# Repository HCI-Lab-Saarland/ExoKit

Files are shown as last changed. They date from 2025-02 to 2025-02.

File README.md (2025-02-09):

# ExoKit: 
## A Toolkit for Rapid Prototyping of Interactions for Arm-based Exoskeletons 
### (ACM CHI 2025, Released Code)

**[Marie Muehlhaus](https://hci.cs.uni-saarland.de/people/marie-muehlhaus/)**, **[Alexander Liggesmeyer](https://cispa.de/de/people/c01alli)**, **[Jürgen Steimle](https://hci.cs.uni-saarland.de/people/juergen-steimle/)**

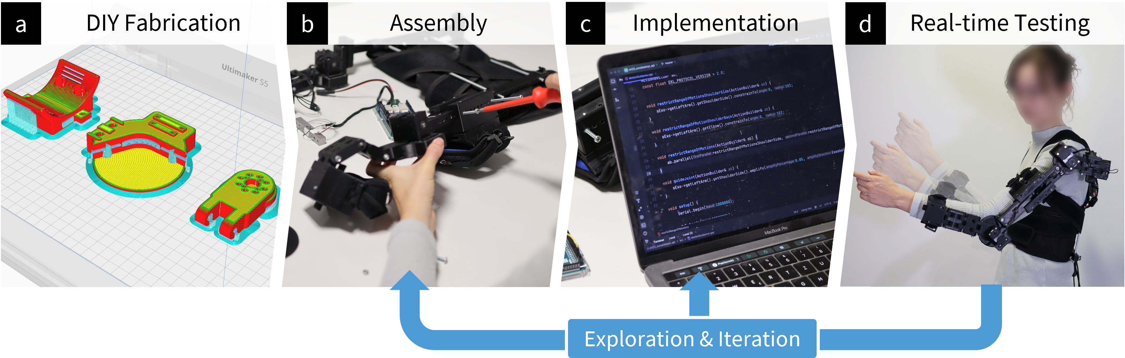
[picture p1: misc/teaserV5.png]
ExoKit Teaser Image


### Abstract
Exoskeletons open up a unique interaction space that seamlessly integrates users' body movements with robotic actuation. Despite its potential, human-exoskeleton interaction remains an underexplored area in HCI, largely due to the lack of accessible prototyping tools that enable designers to easily develop exoskeleton designs and customized interactive behaviors. We present ExoKit, a do-it-yourself toolkit for rapid prototyping of low-fidelity, functional exoskeletons targeted at novice roboticists. ExoKit includes modular hardware components for sensing and actuating shoulder and elbow joints, which are easy to fabricate and (re)configure for customized functionality and wearability. To simplify the programming of interactive behaviors, we propose functional abstractions that encapsulate high-level human-exoskeleton interactions. These can be readily accessed either through ExoKit's command-line or graphical user interface, a Processing library, or microcontroller firmware, each targeted at different experience levels.
Findings from implemented application cases and two usage studies demonstrate the versatility and accessibility of ExoKit for early-stage interaction design. 

[Read full article](https://doi.org/10.1145/3706598.3713815).

---
## Fabrication & Assembly Instructions
ExoKit comprises 3d printable modular components.

The following figure presents an overview of the main exoskeleton components:
<p float="left">
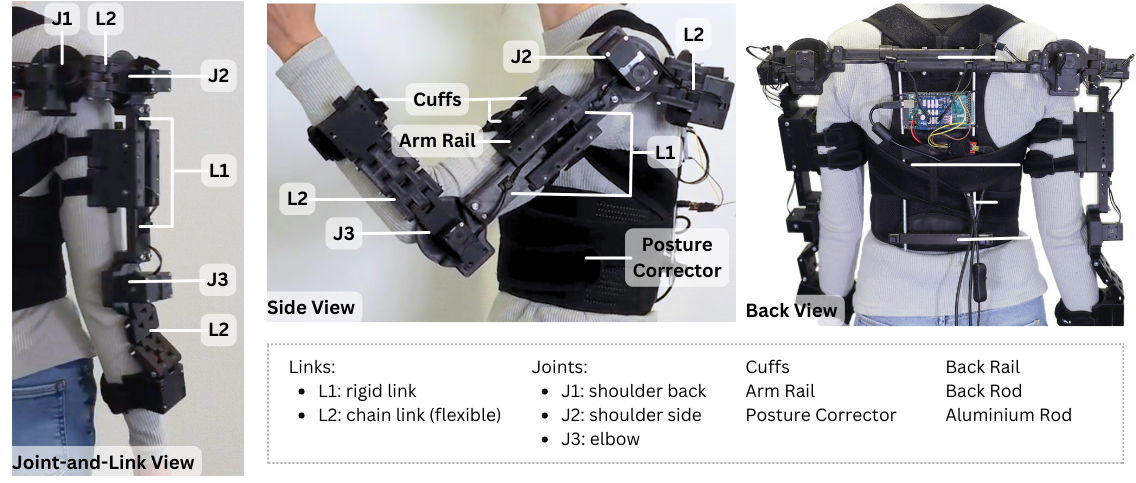
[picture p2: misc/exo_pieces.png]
  
</p>

Detailed instructions for fabrication and assembly can be found in user manual chapter 2 and 3.

## Installation Instructions and Software Usage

ExoKit provides access to pre-implemented functionalities. These comprise basic functions and five augmentation strategies. They are conceptually organized in a two-dimensional space:

<p float="left">
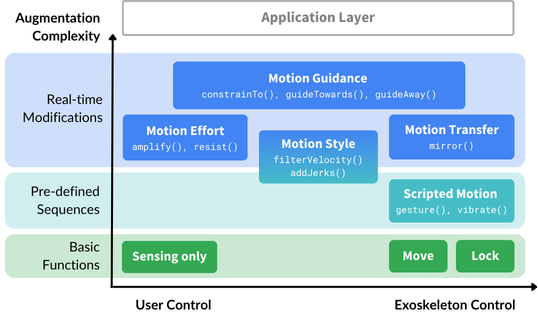
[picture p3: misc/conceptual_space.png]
  
</p>

These functionalities are accessible through different programming interfaces:
<p float="left">
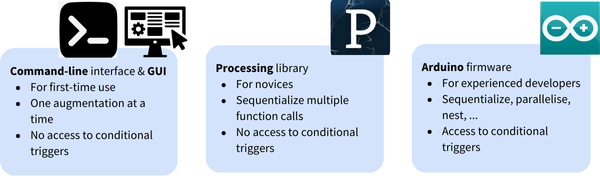
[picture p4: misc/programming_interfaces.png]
  
</p>

Please refer to user manual chapter 2 and 4-7 for more details.

---

## Citation
If you find our article, released hardware or software useful, please cite our work:

```bibtex
@inproceedings{exoKit,
author = {Muehlhaus, Marie and Liggesmeyer, Alexander and Steimle, J\"{u}rgen},
title = {ExoKit: A Toolkit for Rapid Prototyping of Interactions for Arm-based Exoskeletons},
year = {2025},
isbn = {979-8-4007-1394-1/25/04},
publisher = {Association for Computing Machinery},
address = {New York, NY, USA},
url = {https://doi.org/10.1145/3706598.3713815},
doi = {10.1145/3706598.3713815},
booktitle = {Proceedings of the 2025 CHI Conference on Human Factors in Computing Systems},
location = {Yokohama, Japan},
series = {CHI '25}
}
```

---

## Contact

Please contact [Marie Muehlhaus](https://hci.cs.uni-saarland.de/people/marie-muehlhaus/) if you have any questions about ExoKit for your use.

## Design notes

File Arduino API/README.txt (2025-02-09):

Software Setup:
1.	Download the code from this folder (“Arduino API“)
2.	Install CLION (or similar) and follow existing online guides to set up the platformIO extension. Test the successful installation with a simple Arduino program (you can find examples online).
3.	Install the required plugins in CLION:
  o	Serial Port Monitor Plugin: https://plugins.jetbrains.com/plugin/8031-serial-port-monitor
  o	PlatformIO Plugin for CLion: https://plugins.jetbrains.com/plugin/13922-platformio-for-clion  
4.	Open the project as a platformIO project with CLION.
  o	To work with the Arduino Mega, PlatformIO must be set up for megaatmega2560. We provide the suitable platformio.ini file as part of the downloaded code. The platformio.ini contains further library dependencies, such as Dynamixel2Arduino, DynamixelShield, HX711, LinkedList, TaskManagerIO.
5.	Build the project.
  o	In case of an error message about undefined references to loop and setup functions, make sure that one (and only one!) of the example programs in the src folder is commented in.
  o	In case of error messages about libraries not being available for the system, the library dependencies listed in platform.ini (“lib_deps”) might need to be adjusted to fit your system.

You can find an example video for setting up the platformIO project in CLION in the repo’s video folder (“Software Installation PlatformIO”). 

For details about the software and a quick start guide please refer to Chapter 2 of the user manual.
Fpr more details about how to program interactive behavaior with the Arduino API, please refer to Chapter 7 of the user manual.

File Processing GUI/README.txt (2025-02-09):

Processing GUI setup:
1.	Download the GitHub code from this folder (“Processing GUI”) and “Arduino API” (https://github.com/HCI-Lab-Saarland/ExoKit/tree/main/Arduino%20API). 
2.	Download Processing. The authors used version 4.3.
3.	Follow the installation guide for the Arduino API.
4.	Open processing_gui.pde.

The user manual provides further explanation on the usage of the GUI and an example of how to configure the exoskeleton in the Arduino API accordingly (Chapter 5).
All functions and parameters available in the GUI are documented in the user manual (Chapter 5).

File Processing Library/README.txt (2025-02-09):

Processing Library setup:
1.	Download the GitHub code from this folder (“Processing Library”) and “Arduino API” (https://github.com/HCI-Lab-Saarland/ExoKit/tree/main/Arduino%20API). 
2.	Download Processing. The authors used version 4.3.
3.	Install the library.
4.	Follow the installation guide for the Arduino API.

The user manual provides further explanation on the usage of the library and an example of how to configure the exoskeleton in the Arduino API accordingly (Chapter 6).
All functions, signatures and parameters available in the library are documented in the user manual (Chapter 6).

The exokit Processing library comes with one sample sketch, which shows how to configure an exoskeleton and call functions.
Prerequisites for successfully running the example sketch:
- The physical prototype is correctly configured (right arm with active shoulder side and elbow joints).
- The exoskeleton is configured correctly in the Arduino API and the serial connection is active.
- The correct serial port is entered in the Processing code.
The user manual provides an explanation and example of how to configure the exoskeleton in the Arduino API accordingly (Chapter 6)

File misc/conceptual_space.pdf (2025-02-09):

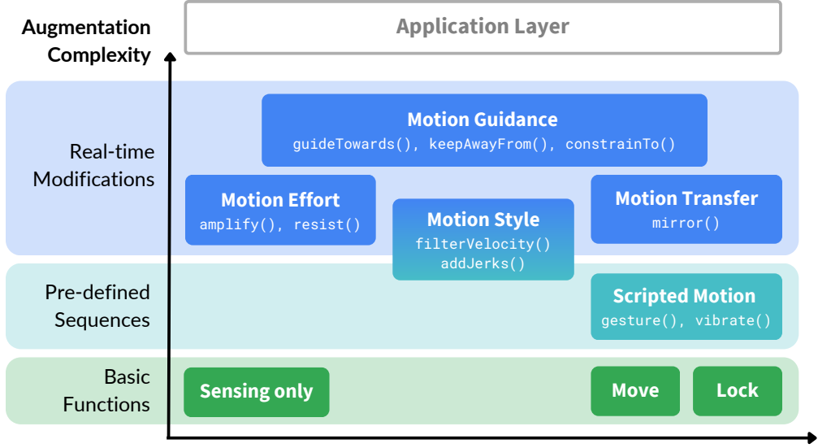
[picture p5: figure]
Sensing only; Move; Lock; Motion Effort; amplify(), resist(); Motion Style; filterVelocity() addJerks(); Motion Transfer; mirror(); Motion Guidance; Application Layer; Scripted Motion; gesture(), vibrate(); Basic Functions; Pre-defined Sequences; Real-time Modifications; Augmentation Complexity

guideTowards(), keepAwayFrom(), constrainTo()

User Control | Exoskeleton Control

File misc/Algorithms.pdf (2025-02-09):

## ExoKit: A Toolkit for Rapid Prototyping of Interactions for Arm-based Exoskeletons

Marie Muehlhaus, Alexander Liggesmeyer, J¨urgen Steimle
Supplemental Material: Algorithms

This supplemental material contains the pseudocode for the algorithms presented in section 4 of the paper, organized by the higher-level motion augmentation strategies. The algorithms build on the following basic functions:

- moveTo(ji
, θi

, υ) moves the joint ji towards a target angle θi with a user-specified velocity υ. All angles are absolute unless explicitly stated otherwise. The function internally checks if the goal angle is beyond a joint’s calibrated range of motion (RoM). If so, the joint would be moved just towards the bound but never beyond. Unless the torque was updated before

(see update torque(ji

, τ )), the motor will be moved with the largest possible torque.

- lock(ji) locks the joint ji
in place. unlock(ji) unlocks the joint ji
- update torque(ji
, τ ) ensures the motor of joint ji
is moving with the specified torque τ ; if τ = 0, then the the torque is disabled. torque is enabled(ji) and torque is disabled(ji) indicate whether τ > 0 and τ = 0, respectively.
- get angle(ji), get velocity(ji), get direction(ji) return the current joint angle, velocity, and movement direction (extension/adduction, flexion/abduction, or both) of ji
- get max velocity(ji) returns the maximum velocity that the motor attached to ji can provide.
- get upper RoM(ji) and get lower RoM(ji) return the maximum and minimum angles of ji

’s calibrated range of motion

- is moving(ji) indicates whether ji
is currently moving.
- parallel(s1, . . . , sk) executes k statements s1, . . . , sk in parallel (e.g., two moveTo(·) at the same time).

In the following, we refer to the joint modules attached to the elbow (flexion-extension), side (flexion-extension) and back (abduction-adduction) of the shoulder as jelbow, jsside, and jsback. Without loss of generality, in the following, we assume that (1) D ∈ {“extension”, “flexion”, “both”} for any direction D and (2) ji ∈ {jelbow, jsside}. We leave out code for D ∈ {“adduction“, “abduction“} and ji = jsback which works analogously to extension and flexion and the other joints.

Further, we decided on the values of constants in the code after doing preliminary tests in the research team. This refers to, for instance, dirChangeSuspensionT ime (amplify) and linearGrowth (resist).

All algorithms except the one for the waving gesture can also have an optional condition as input. In these algorithms, while-loops will run until they are aborted through this user-defined condition, such as a timer, or an emergency shutdown. To keep the pseudocode abstract, we do not include this input in the require parameters and only state the conditions explicitly if needed.

Please note that the algorithms represent the logic of the implemented functions in the form of readable pseudocode, which abstracts away the details of specific programming languages. Our implementation was realised in C++ with an event-based architecture and dedicated Condition and Action classes. The pseudocode below therefore looks different from the actual program structure.

## 1 Scripted Motions

Wave This function executes a sequence of movements to perform a waving gesture with the arm.

Algorithm 1 Wave
Require: exoskeleton arm with active joints at the elbow, shoulder side and back: jelbow,jsback,

jsside
1: parallel(moveTo(jelbow, 90, 70), moveTo(jsside, 0, 70), moveTo(jsback, 90, 70))

2: parallel(lock(jsside), lock(jsback), moveTo(jelbow, 45, 50))
3: moveTo(jelbow, 90, 50)
4: moveTo(jelbow, 45, 50)
5: moveTo(jelbow, 90, 50)
6: moveTo(jelbow, 45, 50)

7: parallel(unlock(jsside), unlock(jsback))

Vibrate This function generates a vibrating sensation at a joint ji through rapid back-and-forth movements of adjustable amplitude and frequency. The function will loop until aborted. An abort can be triggered by a user defined condition or an emergency shutdown.

Algorithm 2 Vibrate
Require: joint ji

, amplitude amp, frequency f 1: υrequired ← min(4f · amp, get max velocity(ji)) ▷ ensure that υrequired does not exceed the max. available velocity of ji
2: while not aborted do ▷ the loop will run until it is aborted through a user-defined condition, such as a timer, or an emergency shutdown
3: | moveTo(ji

, 2 · amp, υrequired, relative)

4: | moveTo(ji

, −2 · amp, υrequired, relative)

## 2 Motion Transfer

Mirror The mirror function facilitates motion transfer between two exoskeletons or joint instances, where in every time interval, the state of the source joints js is read and the target joints jt are moved accordingly. Users can optionally scale the motion up or down by a user-defined factor, while the moveTo(·) function internally ensures that the scaled motion does not exceed the user’s calibrated limits of their range of motion. The function runs in a loop until it is aborted.

Algorithm 3 Mirror
Require: target joint jt

, source joint js, scale factor f
1: while not aborted do
2: | moveTo(jt

, f · get angle(js), get max velocity(ji))

## 3 Effort Modulation

Amplify Amplify applies a torque in a user’s inherent motion, while preserving the user’s ability to freely navigate in space. The function includes parameters that allow designers to adjust the assistive torque τamp and to specify whether the strategy should be continuously active or only triggered when the user moves in a certain direction D ∈ {“flexion”, “extension”, “both”}. To avoid false activations triggered by slight jerks of the user or amplifying the user beyond a safe speed, the function additionally includes parameters that define the minimum and maximum speed where the amplification should start or pause respectively. The function runs in a loop until it is aborted.

Algorithm 4 Amplify
Require: joint ji

, amplifying torque τamp, supported movement direction D, minimum velocity to start amplification υstart, max. velocity to which arm should be amplified υstop
1: dirChangeSuspensionT ime ← 200 ▷ a constant that tunes the sensitivity to direction changes (in ms)
2: lastDirChangeT ime, lastT orqueEnable ← 0
3: f irstStep ← true
4: currentDirIsFlex ← f alse
5: while not aborted do
6: | if (|get velocity(ji)| > |υstop|) then
| /* stop amplification because ji moves too fast */
7: | update torque(0)
8: | else if (|get velocity(ji)| > |υstart| ∧ D ∈ {get direction(ji)} ∪ {“both′′} then
| /* ji moves sufficiently fast in desired direction */
9: | dirIsFlexU pdated ← get direction(ji) = flexion
10: | if currentDirIsFlex ̸= dirIsFlexU pdated then
| /* because direction has changed, we pause the amplification */
11: | currentDirIsFlex ← dirIsFlexU pdated
12: | if f irstStep then
13: | f irstStep ← f alse
14: | else
15: | lastDirChangeT ime ← millis()
16: | update torque(0)
17: | if lastDirChangeT ime + dirChangeSuspensionT ime < millis() then
| /* because enough time has passed between direction change and now, we resume ampli-
| fication */
18: | if torque is disabled(ji) then
| /* amplify by letting ji pull the user with τamp towards the end of user’s RoM. */
19: | update torque(ji , τamp)
20: | lastT orqueEnable ← millis()
21: | if currentDirIsFlex then
22: | moveTo(ji , get upper RoM(ji), υstop)
23: | else
24: | moveTo(ji , get lower RoM(ji), υstop)
25: | else if lastT orqueEnable + dirChangeSuspensionT ime < millis() then
| /* eventually pause amplification if ji moves too slow or in opposite direction */
26: | update torque(0)

Resist Resist applies a torque opposite to a user’s inherent motion, while preserving the user’s ability to freely navigate in space. The function includes parameters that allow designers to adjust the resistive torque τres and to specify whether the strategy should be continuously active or only triggered when the user moves in a certain direction D ∈ {“flexion”, “extension”, “both”}. To avoid that the user is slowed down below a specific speed, the function additionally includes a parameter that defined the minimum speed. The function runs in a loop until it is aborted.

Algorithm 5 Resist
Require: joint ji
, resisting torque τres, supported movement direction D, min. velocity to which arm should be slowed down υstop
1: linearGrowth ← 100 ▷ a constant that tunes the adaptation to velocity changes (in deg/sec) 2: f irstStep ← true
3: currentDirIsFlex ← f alse
4: while not aborted do
/* adapt the resistance to ji’s velocity by τfraction ∈ [0, 1] percent; the slower the motion, the weaker the resistance, so that the user is not abruptly slowed down when the resistance is triggered. */
5: | τfraction ← min(1, max(0, |get velocity(ji)|−|υstop|
|υstop|+linearGrowth | ))
6: | τadapt ← τres · τfraction
7: | if |get velocity(ji)| < |υstop| then | ▷ pause resistance if ji is too slow
8: | update torque(0)
9: | else if D ∈ {get direction(ji)} ∪ {“both′′} then
/* if ji moves sufficiently fast in desired direction, provide resistance; if user is not moving anymore in the same direction as in the previous loop iteration, update behavior */
10: | dirIsFlexU pdated ← get direction(ji) = “flexion”

/* resist by letting ji continuously try to push the user towards ji, making it hard to
| move away from this fix point */
11: | update torque(ji
| , τadapt) | ▷ update applied torque now
12: | if torque is disabled(ji) then
13: | moveTo(ji
| , get angle(ji), υstop) | ▷ torque was disabled, so update fix point
14: | else if currentDirIsFlex ̸= dirIsFlexU pdated then
15: | currentDirIsFlex ← dirIsFlexU pdated
16: | if firstStep then
17: | f irstStep ← f alse
18: | else
19: | moveTo(ji
| , get angle(ji), υstop) | ▷ direction changed, so update fix point
20: | else
21: | update torque(0)

## 4 Motion Style

Jerks The jerk function introduces short exoskeleton movements at a user-specified velocity, with varying magnitude and at varying time intervals, creating brief perturbations in the user’s inherent motion. The loop runs until aborted or the user-specified number of jerks is performed.

Algorithm 6 Jerk

Require: joint ji

, min./max. jerk size θminJerk/θmaxJerk, min./max. time interval between jerks tmin/tmax, jerk velocity υ, number of jerks nrJerks
1: lastLoopRun, lastJerk ← millis()
2: currentW aitDuration ← 0
3: jerksP erformed ← 0
4: while not aborted ∧ jerksP erformed < nrJerks do
5: | currentT ime ← millis()
6: | deltaLastLoopRun ← currentT ime − lastLoopRun
7: | lastLoopRun ← currentT ime
8: | if ¬is moving(ji) then | ▷ no jerks if user does not move
9: | lastJerk ← lastJerk + deltaLastLoopRun
10: | continue
11: | if ¬(currentT ime > lastJerk + currentW aitDuration) then ▷ not yet time for the next
| jerk
12: | continue
13: | lastJerk ← millis()
14: | currentW aitDuration ← random([tmin, tmax])
15: | valid ← true
16: | repeat
/* randomly search for a valid choice for θjerk, i.e., within the user’s specifications */
17: | jerkDirection ← random({“flexion”, “extension”})
18: | θjerk ← random([θminJerk, θmaxJerk])
19: | if jerkDirection = “extension” then
20: | θjerk ← −θjerk | ▷ a jerk towards extension decreases current angle
21: | if (get angle(ji) + θjerk > get upper RoM(ji)) ∨ (get angle(ji) + θjerk <
| get lower RoM(ji)) then
/* if jerk moves out of calibrated RoM, jerk is invalid */
22: | valid ← false
23: | until valid
24: | moveTo(ji , get angle(ji) + θjerk, υ)
25: | jerksP erformed ← jerksP erformed + 1

Filter Speed Filter speed tries to keep a user’s motion speed within a pre-defined range, by applying assistive torques if they are too slow or resisting ones if they are moving too fast. Designers can fine-tune these effects by setting the velocity range, the forces applied to maintain it and by specifying whether the strategy should be continuously active or only triggered when the user moves in a certain direction D ∈ {“flexion”, “extension”, “both”}. The function runs in a loop until it is aborted.

Algorithm 7 Filter Speed
Require: joint ji

, min. and max. speed υmin and υmax, supported movement direction D, amplifying/resisting torque during flexion τampF lex/τresF lex, amplifying/resisting torque during

extension τampExt/τresExt
1: while not aborted do
2: | if D ∈ {“both”, “extension”} then | ▷ set filter only for the right direction(s)
3: | if |get velocity(ji)| > |υmax| then | ▷ as long as user is too fast, resist
4: | Resist(ji

, τresExt, D, |υmax|) with abort condition |get velocity(ji)| ≤ |υmax| ∨
| get direction(ji) ̸= “extension”
5: | else if |get velocity(ji)| < |υmin| then | ▷ as long as user is too slow, amplify
6: | Amplify(ji

, τampExt, D, 10, |υmin|) with abort condition |get velocity(ji)| ≥
| |υmin| ∨ get direction(ji) ̸= “extension”
7: | if D ∈ {“both”, “flexion”} then
8: | if |get velocity(ji)| > |υmax| then
9: | Resist(ji

, τresF lex, D, |υmax|) with abort condition |get velocity(ji)| ≤ |υmax| ∨

| get direction(ji) ̸= “flexion”
10: | else if |get velocity(ji)| < |υmin| then
11: | Amplify(ji

, τampF lex, D, 10, |υmin|) with abort condition |get velocity(ji)| ≥
| |υmin| ∨ get direction(ji) ̸= “flexion”

## 5 Motion Guidance

Constrain to This function constrains the range of motion of a joint ji to an area around an absolute angle θi with range ϵ. As soon as the user attempts to move beyond this range, the exoskeleton tries to move the user back to the boundary, thereby keeping the joint within the specified limits. The function runs in a loop until it is aborted.

Algorithm 8 Constrain to
Require: joint ji

, central angle θi
, range ϵ
1: while not aborted do
2: | if get angle(ji) ≤ θi − ϵ then
3: | goalAngle ← θi − ϵ + 0.55 | ▷ move the user back into the allowed area
4: | moveTo(ji

, goalAngle, get max velocity(ji))
5: | else if get angle(ji) ≥ θi + ϵ then
6: | goalAngle ← θi + ϵ − 0.55
7: | moveTo(ji

, goalAngle, get max velocity(ji))

Guide Towards This function guides the user towards an area centered around θi with range ϵ. The exoskeleton applies assistive torques τamp when moving towards the desired area and resists with τres otherwise. The function runs in a loop until it is aborted.

Algorithm 9 Guide towards
Require: joint ji

, central angle θi

, range ϵ, amplifying torque τamp, resisting torque τres 1: while not aborted do
2: | if get angle(ji) ≥ θi + ϵ then | ▷ if above upper bounds
3: | while get angle(ji) ≥ θi + ϵ do | ▷ not back in motion range
/* to get back in the area, resist during flexion and amplify during extension */
4: | if get direction(ji) = “flexion” then | ▷ If user moves further away, resist
5: | Resist(ji

, τres, “flexion”, 0) with abort condition get direction(ji) ̸= “flexion”
6: | else | ▷ If user approaches the area, amplify
7: | Amplify(ji

, τamp, “extension”, 0, get Max Velocity(ji)) with abort condition get angle(ji) < θi + ϵ ∨ get direction(ji) ̸= “extension”
8: | else if get angle(ji) ≤ θi − ϵ then | ▷ if below lower bounds
9: | while get angle(ji) ≤ θi + ϵ do | ▷ not back in motion range
/* to get back in area, resist extension and amplify flexion */
10: | if get direction(ji) = “flexion” then
11: | Amplify(ji

, τamp, “flexion”, 0, get Max Velocity(ji)) with abort condition

get angle(ji) > θi + ϵ ∨ get direction(ji) ̸= “flexion”
12: | else
13: | Resist(ji

, τres, “extension”, 0) with abort condition get direction(ji) ̸=
| “extension”

Guide Away This function keeps ji away from the area around θi
, applying resistance with torque τres if the user is approaching the area and assistive torques τamp otherwise. The function runs in a loop until it is aborted.

Algorithm 10 Guide away
Require: joint ji

, central angle θi

, range ϵ, amplifying torque τamp, resisting torque τres 1: while not aborted do

2: | if get angle(ji) ≥ (θi − ϵ) ∧ get angle(ji) ≤ (θi + ϵ) then
/* if ji is in dead area, move it out */
3: | if get angle(ji) ≥ θi then | ▷ if closer to upper side, move out there
4: | moveTo(ji , θi + ϵ + 0.55, 0)
5: | else
6: | moveTo(ji , θi − ϵ − 0.55, 0)
7: | else
/* if ji not in dead area, use amplify an resist to keep ji away from it */
8: | if get angle(ji) > θi + ϵ then
9: | while get angle(ji) > θi + ϵ do ▷ above dead area, prevent user from moving to-
| ward it
10: | if get direction(ji) = “flexion” then
/* support user when moving away from the dead area */
11: | Amplify(ji

, τamp, “flexion”, 0, get Max Velocity(ji)) with abort condition

| get direction(ji) ̸= “flexion”
12: | else
/* prevent user when moving towards the dead area */
13: | Resist(ji

, τres, “extension”, 0) with abort condition get angle(ji) ≤ θi +ϵ∨
| get direction(ji) ̸= “extension”
14: | else if get angle(ji) < θi − ϵ then
15: | while get angle(ji) < θi − ϵ do ▷ below dead area, prevent user from moving to-
| ward it
16: | if get direction(ji) = “flexion” then
17: | Resist(ji

, τres, “flexion”, 0) with abort condition get angle(ji) ≥ θi − ϵ ∨

| get direction(ji) ̸= “flexion”
18: | else
19: | Amplify(ji

, τamp, “extension”, 0, get Max Velocity(ji)) with abort condition get direction(ji) ̸= “extension”

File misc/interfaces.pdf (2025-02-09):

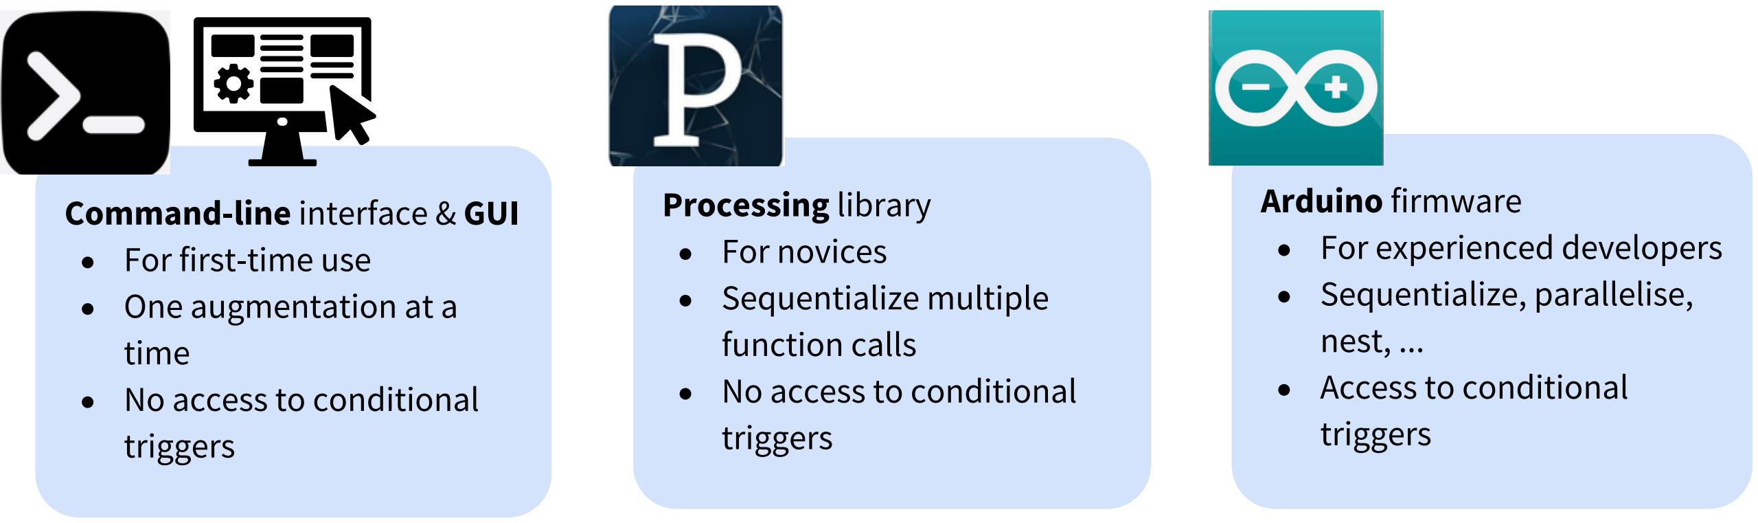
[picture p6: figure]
Processing library For novices Sequentialize multiple function calls No access to conditional triggers; Command-line interface & GUI For first-time use One augmentation at a time No access to conditional triggers; Arduino firmware For experienced developers Sequentialize, parallelise, nest, ... Access to conditional triggers

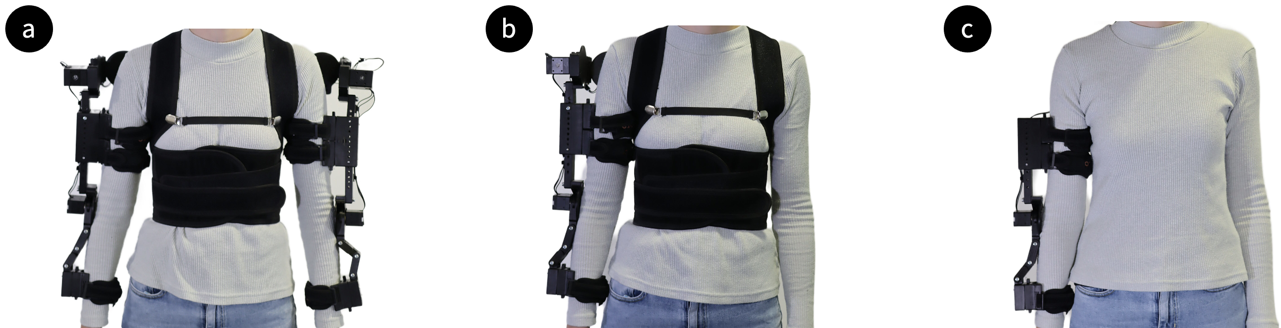
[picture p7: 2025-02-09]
misc/exo_configurations.png

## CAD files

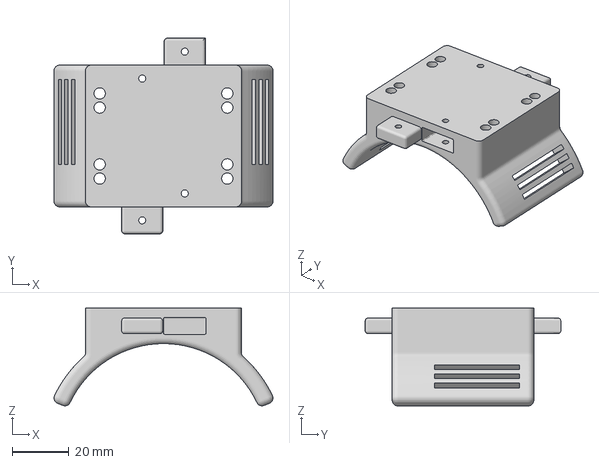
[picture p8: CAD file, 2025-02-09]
3d-prints/forearm_cuff.3mf
77.2 x 69.0 x 34.4 mm

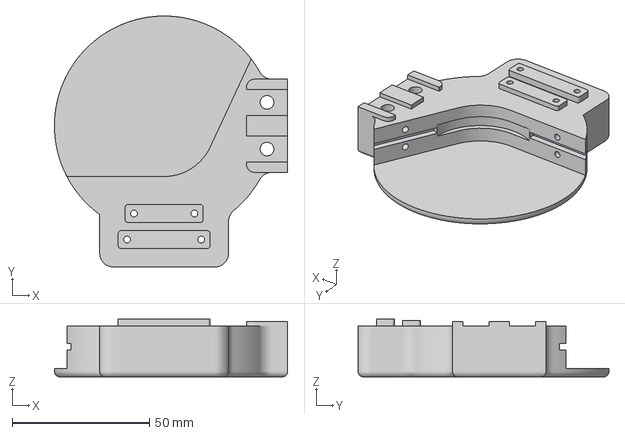
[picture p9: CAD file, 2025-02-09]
3d-prints/left-arm/joint_elbow_l.3mf
85.0 x 91.5 x 21.1 mm

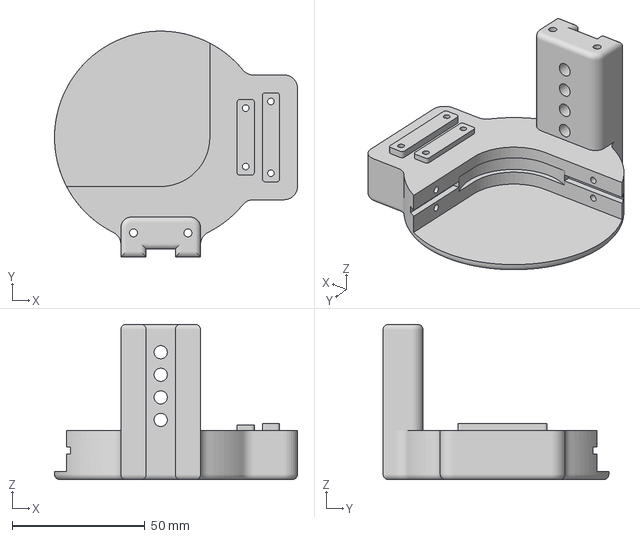
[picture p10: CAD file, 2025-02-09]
3d-prints/right-arm/joint_shoulder_back_r.3mf
91.5 x 85.0 x 58.5 mm

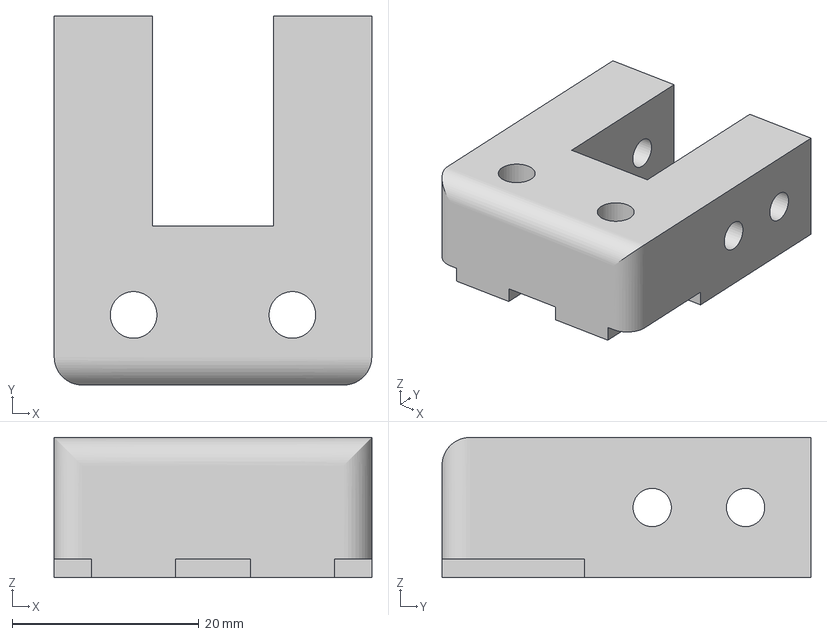
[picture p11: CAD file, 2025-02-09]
3d-prints/loadcell_adapter_joint.3mf
34.0 x 39.5 x 15.0 mm

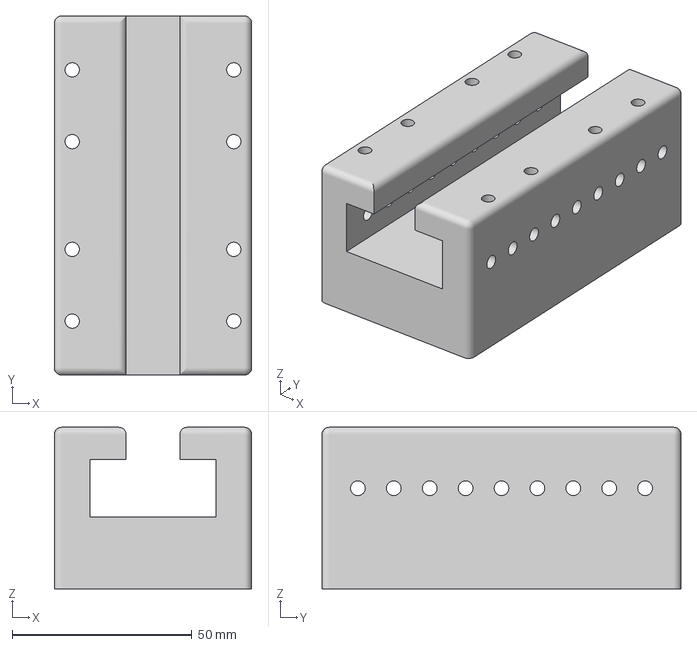
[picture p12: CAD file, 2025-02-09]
3d-prints/arm_rail.3mf
55.0 x 100.0 x 45.0 mm

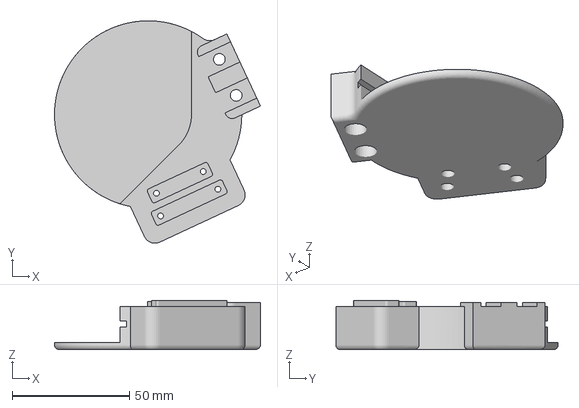
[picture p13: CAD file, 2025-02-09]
3d-prints/left-arm/joint_shoulder_side_l.3mf
88.0 x 94.9 x 21.1 mm

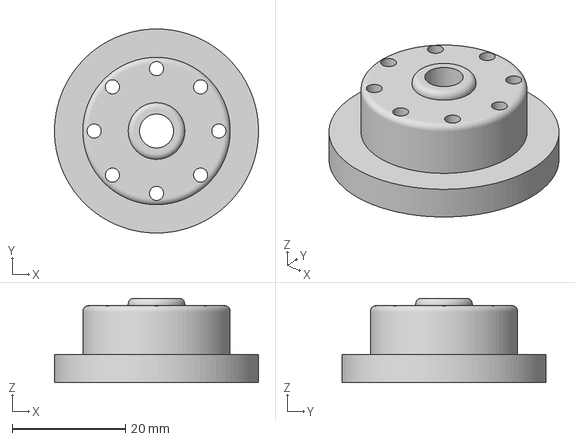
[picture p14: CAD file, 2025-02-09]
3d-prints/servo_dummy_rotor.3mf
36.0 x 36.0 x 14.9 mm

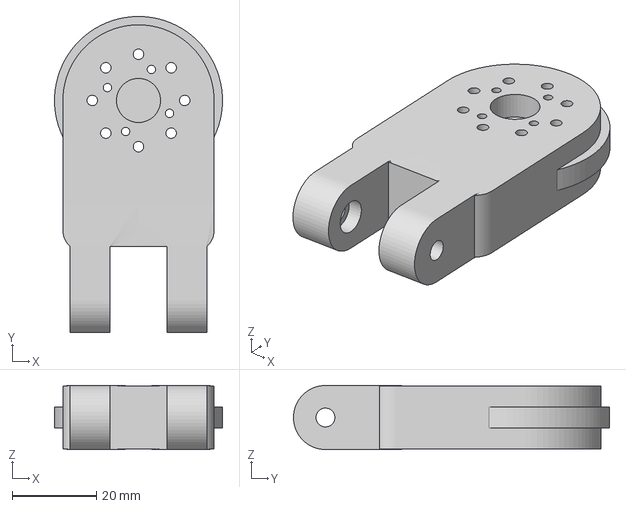
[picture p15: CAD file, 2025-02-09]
3d-prints/rotor.3mf
40.0 x 75.2 x 15.2 mm

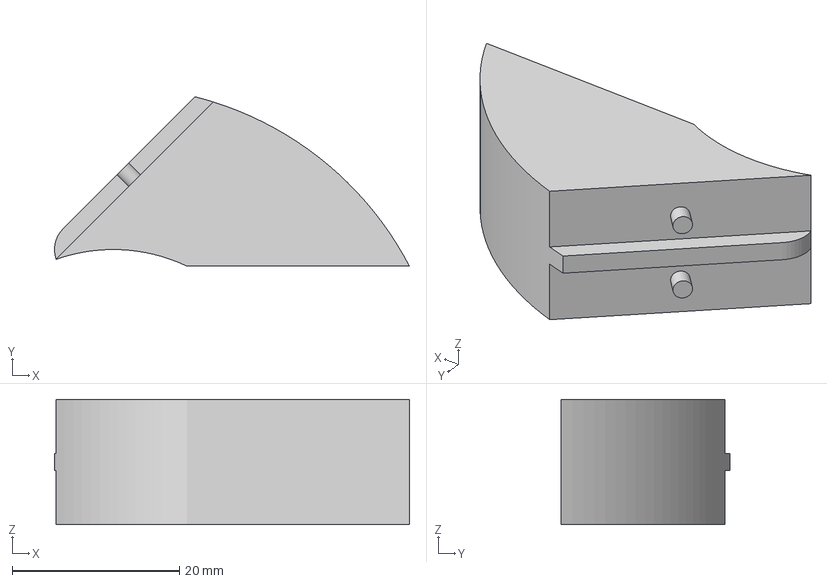
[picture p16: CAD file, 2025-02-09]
3d-prints/restriction_45.3mf
42.5 x 20.3 x 15.0 mm

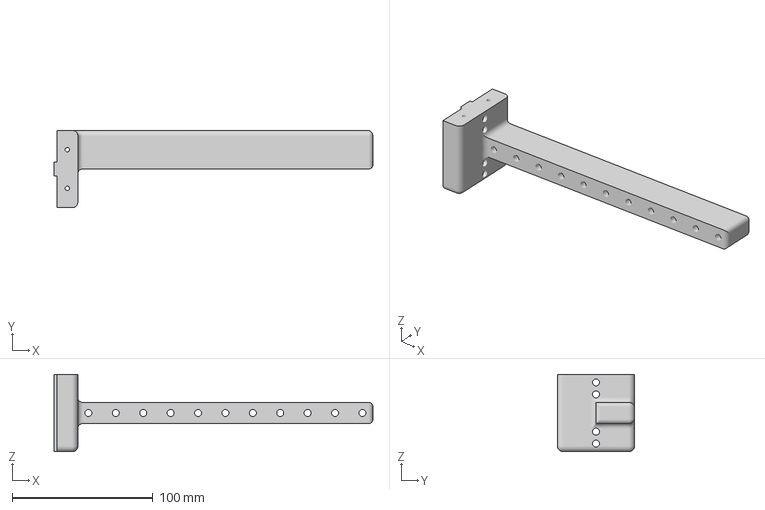
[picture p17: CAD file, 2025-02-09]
3d-prints/back_rail.3mf
227.0 x 55.0 x 55.0 mm

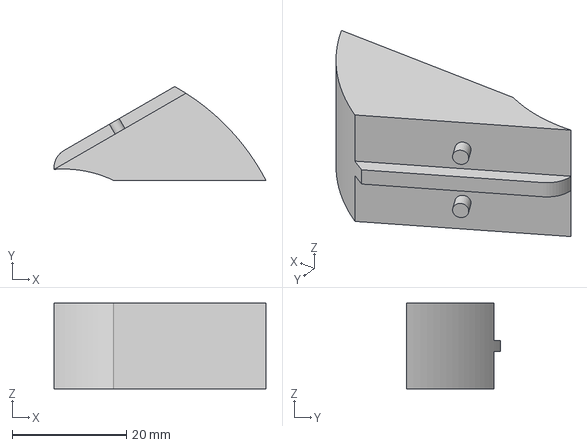
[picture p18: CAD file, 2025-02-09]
3d-prints/restriction_30.3mf
37.1 x 16.4 x 15.0 mm

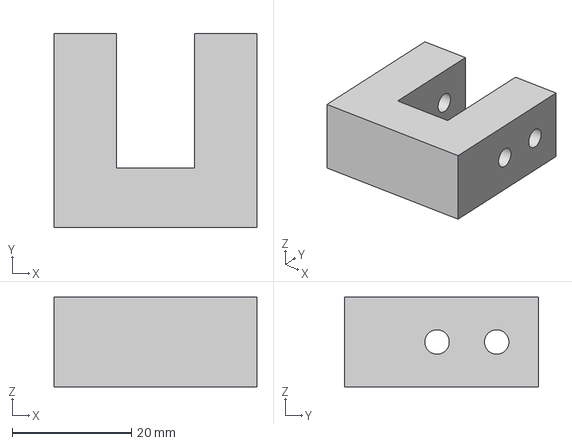
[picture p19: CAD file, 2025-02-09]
3d-prints/loadcell_adapter_rail.3mf
34.0 x 32.5 x 15.0 mm

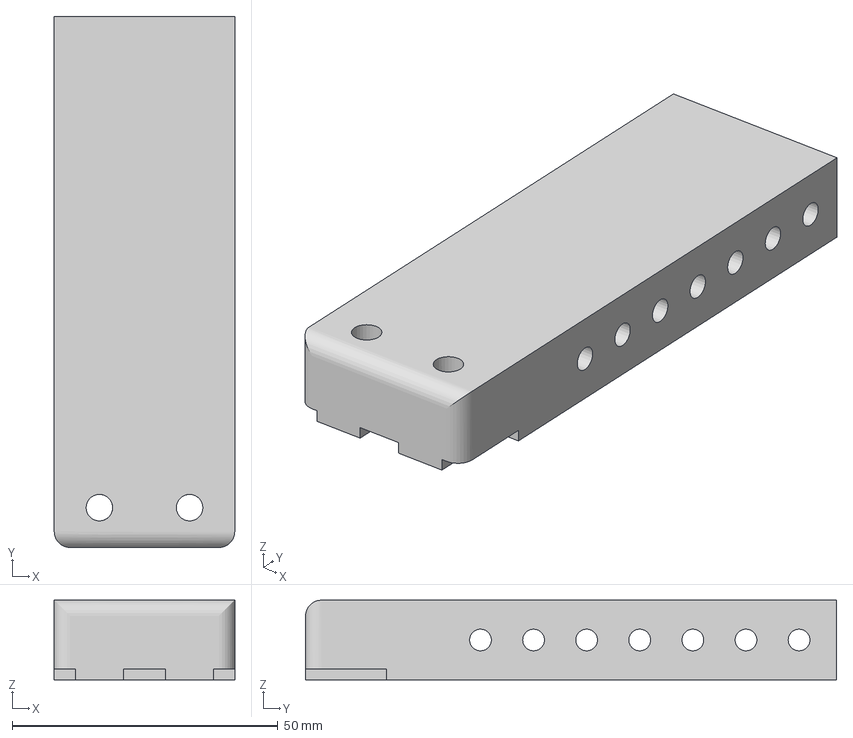
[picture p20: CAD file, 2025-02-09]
3d-prints/joint_rod_long.3mf
34.0 x 100.0 x 15.0 mm

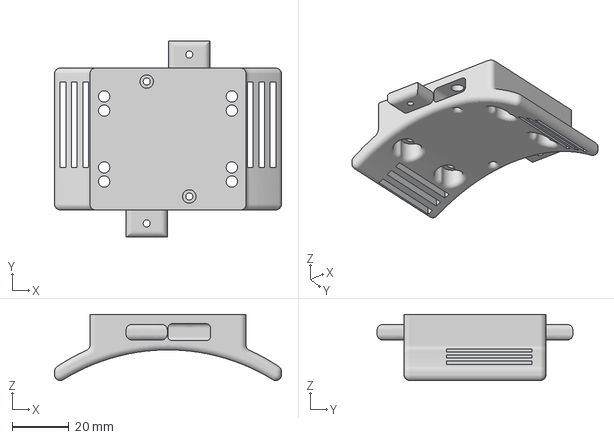
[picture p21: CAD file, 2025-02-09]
3d-prints/arm_cuff_upper_arm.3mf
80.0 x 69.0 x 23.3 mm

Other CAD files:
3d-prints/left-arm/joint_shoulder_back_l.3mf
3d-prints/right-arm/joint_elbow_r.3mf
3d-prints/right-arm/joint_shoulder_side_r.3mf
3d-prints/chain_mf.3mf
3d-prints/chain_mm.3mf
3d-prints/forearm_chain_adapter.3mf
3d-prints/lower_back_rail.3mf
3d-prints/restriction_20.3mf
3d-prints/servo_dummy_outer.3mf

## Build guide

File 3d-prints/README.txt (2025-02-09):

The 3d models were designed with Autodesk Fusion 360. We fabricated the 3D-printed parts with an Ultimaker S5 printer, using ABS filament. We used 100% infill with an octet infill pattern, a normal support structure and 2 mm wall thickness. 

To build the back construction, print:
	2x back_rail
	1x lower_back_rail

To build a 3 DoF actuated left arm (right arm analogous), print:
	Joints: 1x joint_elbow_l, 1x joint_shoulder_back_l, 1x joint_shoulder_side_l, 3x rotor
	Cuffs: 2x arm_cuff_upper_arm, 1x forearm_cuff (the cuff for the forearm is smaller than the upper arm cuff)
	Links: 1x arm_rail, 2x joint_rod_long, 1x forearm_chain_adapter, multiple chain_mf and chain_mm (we recommend at least two chain segments of each type)

If passive joint modules are needed, print:
	1x servo_dummy_outer
	1x servo_dummy_rotor
	1x rotor

If a load cell should be deployed at the upper arm, also print:
	1x loadcell_adapter_joint 
	1x loadcell_adapter_rail 

For more fabrication and assembly information, please refer to the user manual (Chapter 2 & 3).

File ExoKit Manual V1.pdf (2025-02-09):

# EXOKIT

## A TOOLKIT FOR RAPID PROTOTYPING OF INTERACTIONS FOR ARM-BASED EXOSKELETONS

## MARIE MUEHLHAUS, ALEXANDER LIGGESMEYER, JÜRGEN STEIMLE

## USER MANUAL

VERSION 1.0 (NOV 2024)

EXOKIT | A Toolkit for Rapid Prototyping of Interactions for Arm-based Exoskeletons

Project Webpage (including video, link to 3d models, code etc): https://hci.cs.uni-saarland.de/exokit/

Reference:
If you use this toolkit, please reference the scientific publication as follows:
Marie Muehlhaus, Alexander Liggesmeyer, Jürgen Steimle. ExoKit: A Toolkit for Rapid Prototyping of Interactions for Arm-based Exoskeletons. In Proceedings of the 2025 CHI Conference on Human Factors in Computing Systems (CHI ‘25). Yokohama, Japan.
DOI: https://doi.org/10.1145/3706598.3713815

## 1 Table of Contents

### 6 NEXT STEPS IN DESIGN: IMPLEMENT MOTION SEQUENCES WITH THE PROCESSING

7 DEEP DIVE: IMPLEMENTING COMPLEX INTERACTIONS WITH THE ARDUINO LIBRARY......49

APPENDIX E: TERMINAL FUNCTION CALLS | 91

# 1 Introduction

## 1.1 Overview

Exoskeletons open up exciting possibilities for novel interactions that assist, modify, or constrain physical body movements. These wearable devices can be used in Human-Computer Interaction (HCI) research for applications such as motion capture, delivering haptic feedback in virtual reality (VR), and facilitating skill transfer between individuals. For instance, an exoskeleton might serve as a wearable tutor, teaching novices to perform sports like learning a perfect golf swing, or it might enhance safety in hazardous environments, such as preventing accidents on construction sites.

However, the development of functional human-exoskeleton interactions is complex, requiring expertise in mechanical design, motion control, and interaction design. ExoKit is a do-it-yourself toolkit designed to empower designers, makers, and hobbyists in prototyping low-fidelity, functional arm-based exoskeletons. Targeted at users with basic programming and electronics skills, ExoKit offers:

- Modular hardware components for sensing and actuating shoulder and elbow joints. These components are designed to be easy to fabricate, assemble, and reconfigure for customized applications.
- Programming interfaces that simplify programming interactive behaviors.

ExoKit specifically supports users in the early stages of prototyping to creatively explore diverse ideas. Once a promising interaction concept is identified, users can transition to higher-fidelity hardware and software solutions.

Chapter Overview

Chapter 1 provides an introduction to ExoKit’s purpose, some relevant background to human anatomy, application examples to inspire novel users, and recommendations for safe use.

Chapter 2 provides an overview of the required software and hardware, the fabrication and installation steps, and a quick start guide that guides novel users through the basic setup and usage of the hardware in conjunction with the software.

Chapter 3 introduces the modular hardware components, how to combine them, and how to wire the associated sensors and actuators.

Chapter 4 gives an overview of the offered software abstractions and libraries.

ExoKit is an open-source toolkit for low-fi prototyping. We invite the community to use,

Chapter 5-7 explain the usage of the Processing GUI, library, and Arduino API, respectively. It contains guidance on the setup, all function signatures, parameter explanations, sample code and troubleshooting guides. It is recommended to start with the GUI, then move on to the other libraries. It is not necessary to read a chapter in a linear fashion, but to get an overview of the available functions and then use them as needed.

Chapter 8 provides the code of four application examples presented in the published paper.

The appendices include a glossary, a debugging script when working with position encoders to ensure they are set up correctly, a sample script for streaming sensor data including load cell data, a cheat sheet of compatible motor properties and the terminal commands for the command line interface.

## 1.2 Brief Background on Human Anatomy

Understanding the biomechanics of the human upper limbs is crucial for designing effective exoskeletons. Several key properties of the upper limb's anatomy and movement capabilities are particularly relevant in this context. These include the joints’ degrees of freedom (DoFs), range of motion (RoM), and torque settings.

The shoulder joint possesses three DoFs, enabling the following movements: abduction-adduction, flexion-extension, and medial-lateral rotation. The elbow, on the other hand, has two DoFs, allowing for flexion-extension and rotation of the forearm. ExoKit currently supports flexion-extension movements in both the shoulder and elbow (see below Figure b, c), as well as abduction-adduction in the shoulder (Figure a).

The RoM of a joint defines the maximum arc through which the joint can move. These ranges can vary based on factors such as individual anatomical differences and the targeted population. For instance, typical ranges of motion of adults include shoulder abduction and flexion with up to 180 degrees, while shoulder extension reaches up to 60 degrees. Elbow flexion typically spans 150 degrees, with extension returning to a neutral 0-degree position. The RoM supported by ExoKit is visually highlighted in the figure below.

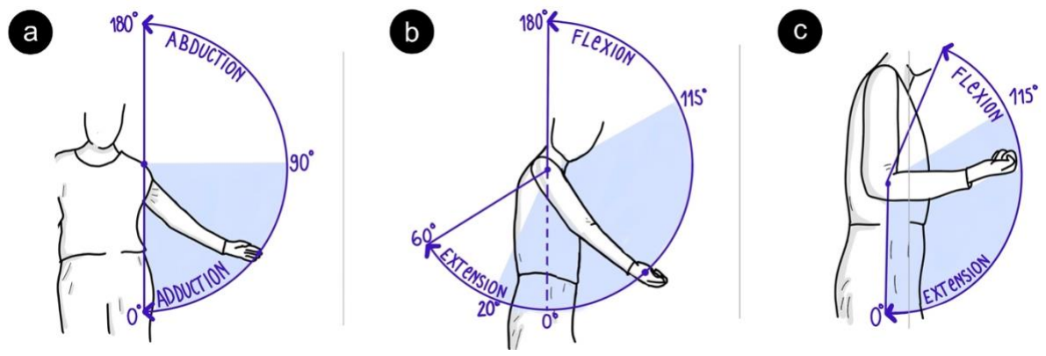
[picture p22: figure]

Another critical factor is the torque required to assist or replicate human joint movements. As such, different applications require different levels of support that are tailored to the user needs. For example, rehabilitation exoskeletons might adjust the amount of support to the patient's progress and muscle strength whereas industrial applications may demand higher torques to handle heavy loads. Directly affecting the user’s body, torques should be carefully selected depending on the intended use case.

## 1.3 Application Examples

These are some ideas to spark your creativity of what to do with ExoKit:

- Improve athletic performance: Use ExoKit to guide or correct your body movements for tasks like throwing a ball. For example, it could help you adopt the right starting position or restrict joint angles to prevent overextension.
- Collaborative art: Work with the exoskeleton to paint on a shared canvas.
- Control a digital game: Use the exoskeleton as a motion-based controller for interactive games. Explore open-source games, such as those available on OpenProcessing, (https://openprocessing.org/sketch/2385209) and adapt them to your exoskeleton setup.
- Compose music through motion: Turn your exoskeleton into a wearable musical instrument using the Processing Sound Library. (https://processing.org/reference/libraries/sound/Sound.html) For instance, you could map joint angles to different notes and movement speed to pitch or volume to create dynamic soundscapes.
- Encourage healthy movement: Design an application that reminds you to move after long periods of inactivity, promoting better posture or overall physical well-being.
- Create a two-player game: For instance, imagine a competitive game where players race to achieve a specific pose. The first to succeed scores a point, while the slower player’s exoskeleton locks briefly as a playful penalty.

In Chapter 8, we present the code of four application cases implemented with ExoKit:

- Designing motion guidance strategies for physical therapy (Figure a)
- Creating kinesthetic feedback to enhance immersion in virtual reality (Figure b)
- Developing a collaborative, body-actuated play experience (Figure c)
- Augmenting a user’s dance style with motion modification (Figure d)

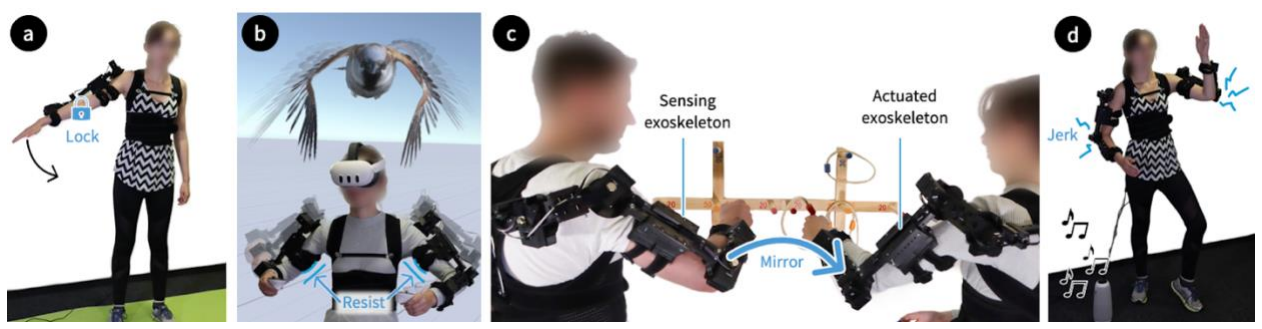
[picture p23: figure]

## 1.4 Safety & Best Practices for Safe Use

Safety is a critical consideration when working with a device that can actuate the body. ExoKit includes three layers of safety—mechanical, software, and user-centered—specifically designed to support novice developers. These layers aim to minimize risks during prototyping:

Mechanical Safety:

- ExoKit provides mechanical safety features to limit the exoskeleton's range of motion. Designers can attach 3D-printed mechanical restrictions to the joints using a simple plug-and-play mechanism (see Chapter 3.1.2). These restrictions physically block the motors from exceeding a predefined range of motion and can be added, removed, or exchanged as needed.

Software Safety:

ExoKit incorporates software routines to monitor the exoskeleton's range of motion in real time. If the system detects that the configured limits are exceeded, it will instantly shut down the system and terminates the current program.

User-Centered Safety:

To give users control over safety, users can include a panic button. When pressed, it instantly shuts down the system and terminates the current program. This feature is especially useful during early development or debugging, allowing users to quickly stop the exoskeleton in case of unexpected behavior.

Other Best Practices

In addition to the built-in safety features, we recommend following these guidelines to ensure safe operation:

- Test interactions off-body first: Before wearing the exoskeleton, test the implemented behavior in a safe, controlled environment to understand how it operates. For instance, lay the exoskeleton on a table or attach it to a mannequin.
- Keep the panic button and/or power switch close: Always keep the panic button close at hand or stay near the power supply, so you or someone nearby can shut off the system quickly if needed.
- Perform proper calibration: During setup, ExoKit will guide you through calibration steps. Follow these carefully to ensure the exoskeleton is properly configured.

# 2 Getting Started

## 2.1 Hardware Components

- 1 Arduino Mega
- 1 Dynamixel Shield for Arduino
- 1 Sparkfun serial basic breakout (CH340C)
- 1-6 motors of the Dynamixel XM series
- 1-3 12 Volt Dynamixel power supplies (Robotis SMPS 12V 5A); depends on the number of motors; we used 3 supplies when 6 motors were involved.
- 1-2 SMPS2Dynamixel adapter (only if several motors are involved)
- Cables:
- USB cable to connect Arduino to PC
- USB cable to connect serial breakout board to PC
- Dynamixel cables to control motors (must match the selected motors)
- Connectors to connect Dynamixel power supply to the Dynamixel shield (e.g., https://www.amazon.de/Connctors-Connector-Security-Surveillance-Transmission/dp/B07QLTWQ66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ÅMÅŽÕÑ&crid=3CR4GU3YRNQK6&keywords=DC+Power+Connector+5.5x2.5mm&qid=1688727928&sprefix=dc+power+connector+5.5x2.5mm%2Caps%2C145&sr=8-23 (https://www.amazon.de/Connctors-Connector-Security-Surveillance-Transmission/dp/B07QLTWQ66?__mk_de_DE=ÅMÅŽÕÑ) )
- If SMPS2Dynamixcel adapter used, additional Dynamixel convertible cables are needed to connect the adapter to the XM motors (X-series-to AX-series adapter cable)
- Jumper wires
- 1 U2D2. Required for initial setup of the Dynamixel motors in the Dynamixel Wizard. Please refer to the Dynamixel user manuals.
- Screws:
- M2x10mm: 2 per small XM motors (2 each)
- M2.5x16mm: 2 per big XM motor and 2 per passive joint module
- M3x60mm: 4 per shoulder and 1 per passive joint module
- M4x40mm: 1 per shoulder
- M4x60mm: 2 per connected chain segments, arm rail (1-2, depends on setup), 4 per arm cuff
- M5X35mm: 2 per connection between joint module and rigid rod
- M4x35-60mm: 4 per load cell (important: cross-check that they fit with the specific load cell model)
- 2 aluminium rods (5mm diameter, 30 mm length) for the back construction (see chapter 2)
- Posture corrector. For a stable attachment, the posture corrector should have a stable and big back part (see chapter 2)
- Velcro tape for attaching the exoskeleton back construction to the posture corrector (see chapter 2)
- Textile arm cuffs. The cuffs must fit through the holes of the printed arm cuffs (max. 3cm width)
- Filament, e.g., ABS

- Optional - bearings, e.g.: https://www.kugellager-express.de/miniatur-kugellager-mr-74-2rs-4x7x2-5-mm. (https://www.kugellager-express.de/miniatur-kugellager-mr-74-2rs-4x7x2-5-mm) They can be inserted in the chain segments for a smoother rotation:
- 2 bearings per joint rod
- 2 bearings per chain adapter at the forearm cuff
- 6 bearings per female chain segment
- 5 bearings per male chain segment
- Optional - sensors:
- 1 Arduino-compatible pushbutton to be used as the emergency button
- Adafruit-based load cells with HX711 ADC chips. Important: should support at least 80 Hz
- Adafruit-based panel mount 10K potentiometer for angle tracking
- Optional – mobile setup. Motors can be powered with the Dynamixel power supplies or a portable power bank. For the latter, we used:
- 1 battery (e.g., https://zeeebattery.com/products/zeee-4s-lipo-battery-3300mah-14-8v-50c-xt60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 Oapf) (https://zeeebattery.com/products/zeee-4s-lipo-battery-3300mah-14-8v-50c-xt60)
- | 1-3 | voltage | converters | to | power | the | motors | & | shield | (e.g.,
https://www.amazon.de/gp/product/B09CYZTM96)
- | 1 | voltage | converter | to | power | the | Arduino | (e.g.,
https://www.amazon.de/gp/product/B09B7XZYJQ?th=1)
- Lipo voltage tester
- Optional to cover the voltage converters & co: a plastic box large enough to fit the components

## 2.2 Hardware: Fabrication

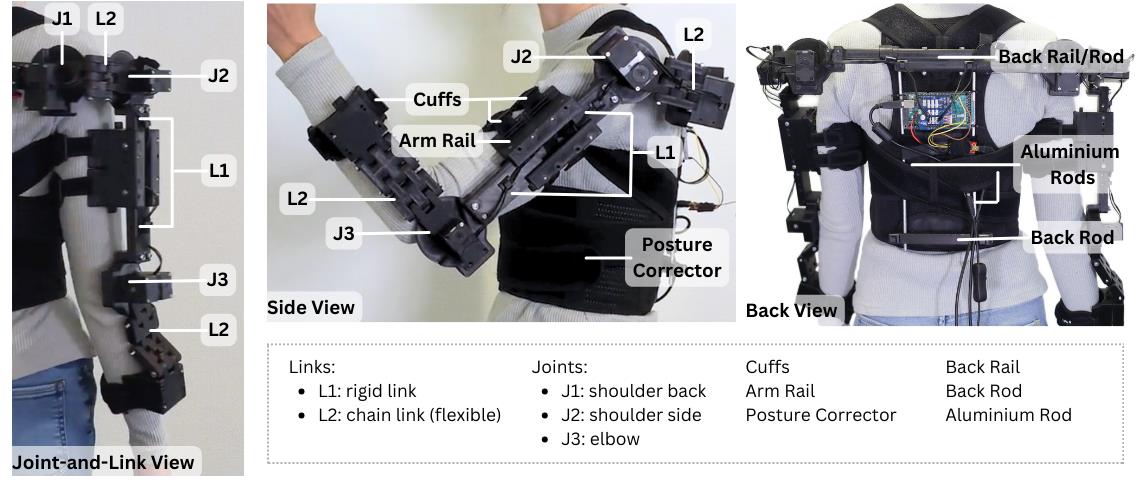
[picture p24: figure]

Step 1: 3d printing

The 3d models were designed with Autodesk Fusion 360. We fabricated the 3D-printed parts with an Ultimaker S5 printer, using ABS filament, 100% infill with an octet infill pattern, a normal support structure and 2 mm wall thickness.

To prepare the back construction, print:
- 2x back_rail
- 1x lower_back_rail

To build a 3 DoF actuated left arm (right arm analogous), print:
- | Joints: | 1x | joint_elbow_l, | 1x | joint_shoulder_back_l, | 1x
joint_shoulder_side_l, 3x rotor
- Cuffs: 2x arm_cuff_upper_arm, 1x forearm_cuff (the cuff for the forearm is smaller than the upper arm cuff)
- Links: 1x arm_rail, 2x joint_rod_long, 1x forearm_chain_adapter, multiple chain_mf and chain_mm (we recommend at least two chain segments of each type)

If passive joint modules (cf., Chapter 3) are needed, print:
- 1x servo_dummy_outer
- 1x servo_dummy_rotor
- 1x rotor

If a load cell should be deployed at the upper arm, also print:
- 1x loadcell_adapter_joint
- 1x loadcell_adapter_rail

Step 2: Preparing the fabricated parts

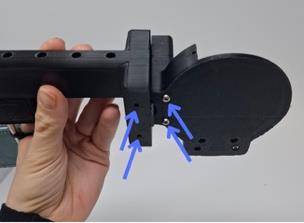
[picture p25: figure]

Stabilization of the shoulder: Insert screws at the left and right ends of the back rail (4 M3x60mm screws per side). These enhance stability of the back construction.

Chain segments: The chain segments and forearm chain adapter are designed to accommodate bearings. The use of bearings helps the chain to move more smoothly. Insert the bearings by pushing them into the holes. Pliers might help to insert the bearings.

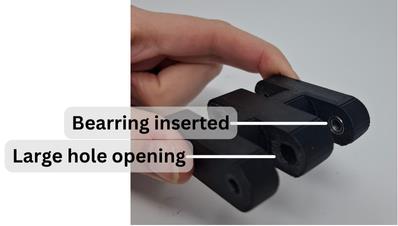
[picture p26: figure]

Preparing the passive joint modules: First, insert the servo_dummy_rotor into the servo_dummy_outer. Next, prevent it from slipping out with the help of a M3x60mm screw.

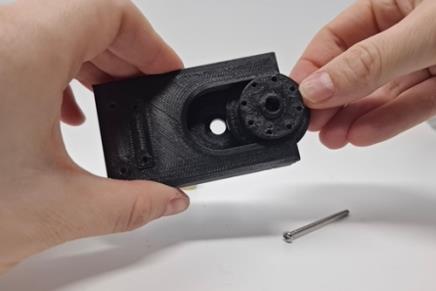
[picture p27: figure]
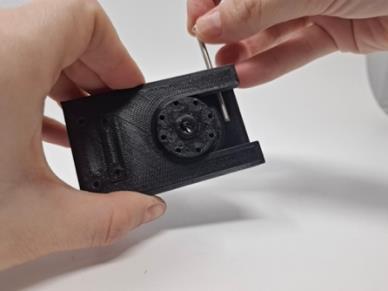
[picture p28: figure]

Arm cuffs: Use M4x60mm screws to screw the upper arm cuffs to the arm rail and the forearm cuff to the forearm chain adapter (see photos below). Finally, attach the textile arm cuffs to the 3d printed cuffs.

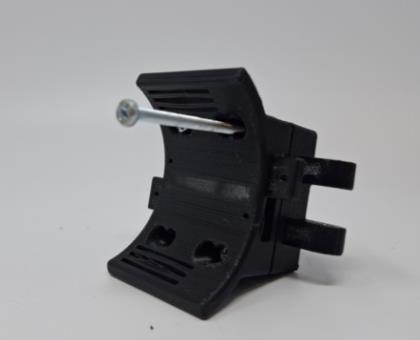
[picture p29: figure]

Assembling the back scaffold: The exoskeleton is held in place through a back construction that is attached to the posture corrector with the help of sewn Velcro tapes. The 3d printed back rails are connected through aluminium rods that were inserted through the holes of the printed rails. Note that the width of the back construction can be adjusted based on which holes the rods are inserted (this affects the alignment of the shoulder joints). The figures below show how the rail and aluminium rods were connected and where the Velcro tapes were sewn to hold the scaffold in place.

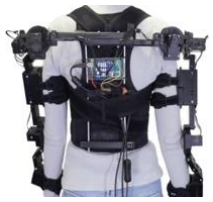
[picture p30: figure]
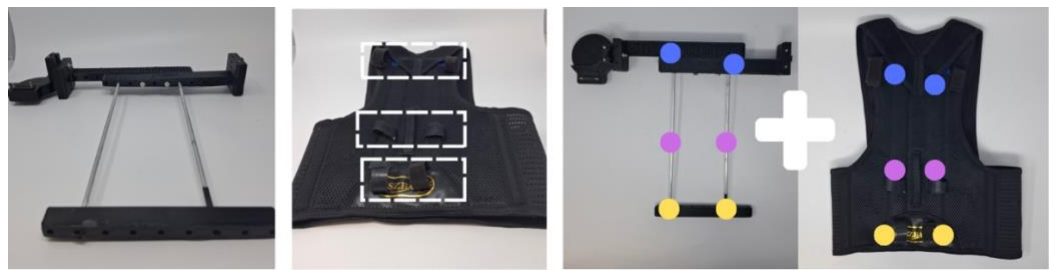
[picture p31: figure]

## 2.3 Software: Installation

Processing GUI

1. To set up the Processing GUI, download the GitHub code from the folders “Processing GUI” and “Arduino API”.
2. Download Processing. The authors used version 4.3.
3. Follow the installation guide for the Arduino API.
4. Open processing_gui.pde.
5. Chapter 5 explains the GUI usage.

Processing library

1. To set up the Processing library, download the GitHub code from the folders “Processing library” and “Arduino API”.
2. Download Processing. The authors used version 4.3.
3. Install the library.
4. Follow the installation guide for the Arduino API.
5. You can find an example program in the download folder (processing_sample).
6. Chapter 6 explains the library usage.

Arduino API

1. To set up the Arduino API, only download the GitHub code from the folder “Arduino API“
2. Follow existing online guides to the platformIO extension for CLION. Test the successful installation with a simple Arduino program (you can find examples online).
3. Install the required plugins in CLION:
- Serial Port Monitor Plugin: https://plugins.jetbrains.com/plugin/8031-serial-port-monitor (https://plugins.jetbrains.com/plugin/8031-serial-port-monitor)
- PlatformIO Plugin for CLion: https://plugins.jetbrains.com/plugin/13922-platformio-for-clion (https://plugins.jetbrains.com/plugin/13922-platformio-for-clion)
4. Open the project as a platformIO project.
- To work with the Arduino Mega, PlatformIO must be set up for megaatmega2560. We provide the suitable platformio.ini file as part of the downloaded code. The platformio.ini contains further library dependencies, such as Dynamixel2Arduino, DynamixelShield, HX711, LinkedList, TaskManagerIO.
5. Build the project.
- In case of an error message about undefined references to loop and setup functions, make sure that one (and only one!) of the example programs in the src folder is commented in.
- In case of error messages about libraries not being available for the system, the library dependencies listed in platform.ini (“lib_deps”) might need to be adjusted to fit your system.
6. You can find a video for setting up the platformIO project (software_installation) in the repo’s video folder (“Software Installation PlatformIO”).
7. Details about the API can be found in chapter 7.

## 2.4 Quick Start Guide: Basic Setup

This section guides you through setting up the Arduino Mega, Dynamixel shield, and serial communication. The basic setup is shown below:

Components

- Arduino Mega: The main microcontroller for controlling the system.
- Dynamixel Shield: Manages communication with Dynamixel motors.
- Serial Communication:
- Serial #1: USB connection to the Arduino for uploading code. ⚠️ Note: This port is blocked during motor operation as it is used for motor communication.
- Serial #2: External serial connection through the serial breakout board from the Arduino to a terminal, allowing commands and data exchange while the Arduino communicates with the shield.

Wiring

- Connect RX of the breakout board to pin 16 (TX2) on the Arduino Mega.
- Connect TX of the breakout board to pin 17 (RX2) on the Arduino Mega.
- Connect GND of the breakout board to any free GND pin on the Arduino Mega.
- Ensure both USB connections (Serial #1 and Serial #2) are connected to the computer.
- Connect the motor directly to the shield.
- Connect an additional power supply to the shield to power the motors later. ⚠️ Be cautious when handling the power supply to avoid damaging the shield or motors.
- While not shown in the photos, you can add an additional Adafruit button, which will serve as an emergency switch. To wire the button, connect one button pin to a digital pin on the Arduino Mega (e.g, pin 50), and the other button pin to any free GND pin on the Arduino Mega.

Turning On and Connecting the Hardware

Before starting, check the following:

- Hardware: Ensure the Dynamixel shield power is off, the Dynamixel shield is in upload mode and the Dynamixel power supply is plugged in. Noth USB cables (Serial #1 and Serial #2) are connected to the computer.
- Software: The software is set up correctly with PlatformIO installed, the ExoKit library imported, and the correct board (Arduino Mega) selected.
1. Turn on the Dynamixel shield power. 🔴 A red LED on the shield should light up (if not already on from a previous session).
2. In the software (e.g., CLion or Arduino IDE), upload the program (for testing the basic setup, see sample code below). Ensure the correct port for uploading code to Arduino is indicated (serial #1, not the one from the breakout board). Wait until the upload succeeded.
3. Once the upload is confirmed, switch the Dynamixel shield to Dynamixel mode.
4. In the software, now select the other serial connection (serial #2) to read the Arduino output and communicate with the board.
5. Press the reset button on the Arduino.
6. A calibration dialog should appear in the terminal. When testing the basic setup, simply confirm with y.

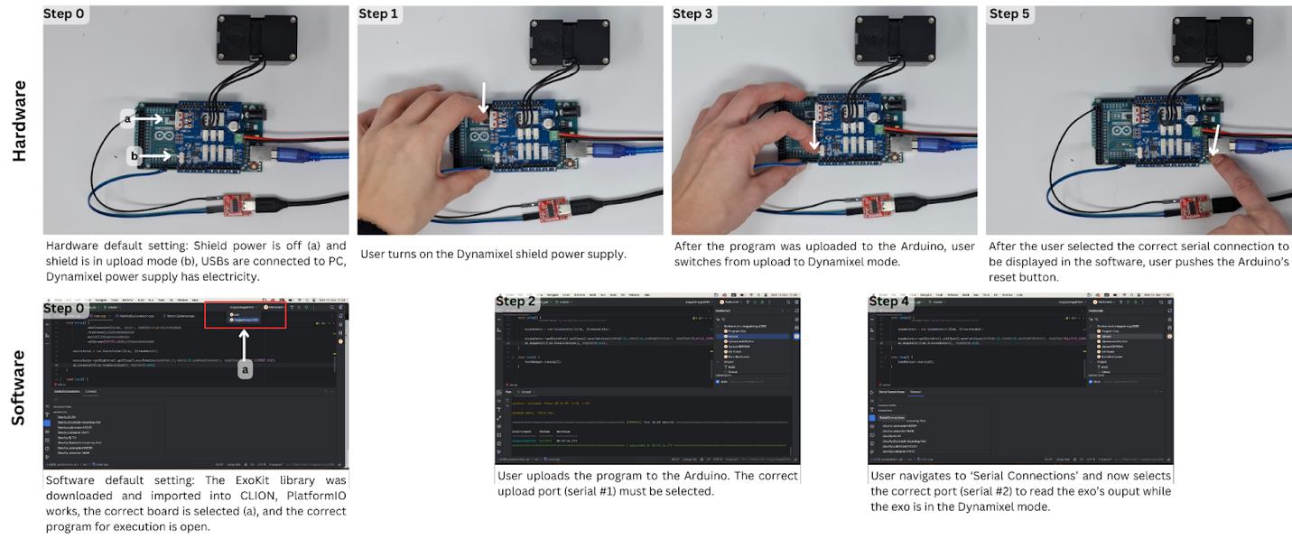
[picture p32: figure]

Testing the Basic Setup

To verify the setup, run the following script in PlatformIO. This script moves the motor by 10 degrees.

⚠️Note: Before running the script, ensure the Dynamixel ID matches the motor. If needed, refer to the Dynamixel Wizard to configure unique IDs and the correct baud rate for your motors (recommended: 1,000,000).

#include "event/simpleactionbuilder/ActionBuilder.h"

#include "exo/ConfiguredEncoder.h"

#include "DynamixelShield.h"

#include "exo/builder/ExoskeletonBuilder.h" #include "event/simpleactionbuilder/Exoskeleton.h"

DynamixelShield dxl;
ExoskeletonHandle* exoHandle;
Exoskeleton* exoskeleton;
ActionBuilder ab;
const float DXL_PROTOCOL_VERSION = 2.0;

void setup() {
Serial.begin(1000000);
dxl.begin(1000000l);
dxl.setPortProtocolVersion(DXL_PROTOCOL_VERSION); dxl.ping(1);
DEBUG_SERIAL.begin(115200);

// TODO change the indicated Dynamixel ID (currently 4) to your //Dynamixel's ID
exoHandle = &ExoskeletonBuilder()
.addRightArm()
.addElbowJoint(dxl, 3, nullptr) .finishArm()
.addEmergencyShutdownButton(50,true) .build()
.calibrate(CREATE);

exoskeleton = new Exoskeleton{ab, *exoHandle};

exoskeleton->getRightArm().getElbow().moveToActive(10,20,5, RELATIVE_CURRENT_POS);
ab.dispatch(ab.trueCondition(), 100);
}

void loop() {
taskManager.runLoop();
}

Troubleshooting

If the setup does not work, check the following:

- Is the power turned on?
- Is the Dynamixel shield in upload mode (for uploading code) or Dynamixel mode (for motor operation)?
- Do the Dynamixel IDs match the IDs indicated in the program? Is the baud rate set to 1,000,000? Use the Dynamixel Wizard and a U2D2 board for reconfiguration if needed. Refer to the Dynamixel’s documentation for more details.
- Is the correct USB serial port selected? If the terminal shows cryptic signs, you may be connected to the wrong port.

# 3 Using the Toolkit: Modular Hardware Components

ExoKit allows the designer to easily adjust the hardware prototype by detaching joints to combine and exchange components, adjust the side and remove or add DoFs to fit designer’s specific project requirements. For instance, designers can construct exoskeletons that support both arms (a), only one arm (b) or the elbow (c). In the following, we detail on exoskeletons key components (link and joint types), and illustrate the assembly of the modular components.

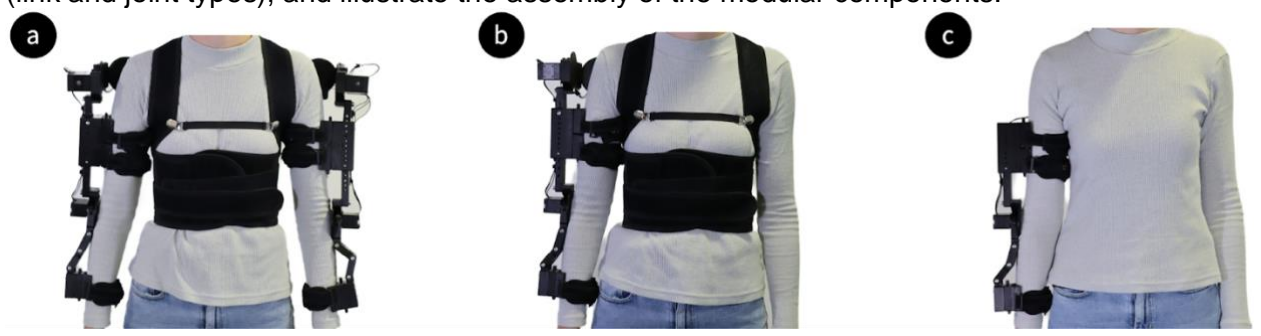
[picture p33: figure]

## 3.1 Components Overview

The exoskeleton comprises several key elements:

Link types

Exoskeleton links are structural components that connect and transmit forces between joints. In ExoKit, we provide two types of 3D-printable passive links. The first is a simple rigid rod, used to stably connect the shoulder and elbow joints (joint_rod_long). The second is a flexible link made of 3d printed chain segments (chain_mm, chain_mf).

Integration of additional sensors

If desired, both the rigid and chain links can be equipped with an additional load cell that captures the torques applied to the joints as they are common sensors deployed in exoskeletons (a, b).

Size-adjustability

The rigid links on the upper arm and back use adjustable mechanisms to accommodate a range of body sizes (c). The chain link can be adjusted to different shoulder circumferences and lower arm lengths by simply attaching or detaching chain segments (d). Finally, the arm cuffs which connect the links to the human arm come in two different sizes, and can be stacked together to provide a larger area that holds the exoskeleton in place.

Joint types

As exoskeletons can be either actuated, act as a sensing device, or be passive, it is crucial for designers to have the flexibility to choose the functionality for their application themselves. To enable hands-on reconfigurability, ExoKit offers three types of interchangeable joint modules:
- Actuated joints (b) comprise an actuator. A joint base (a) serves for mounting a motor. The base is designed to be compatible with all motors of the Dynamixel XM series. These motors inherently offer sensing capabilities (position, velocity). If desired, developers can modify the design of the joint base to include other motors with different dimensions.
- Passive joints (c) simply follow the user's motions, realizing a passive DoF.
- Sensing-only joints (d) measure the exoskeleton angle configuration, through which further motion properties, including velocity and acceleration, can be inferred.
To realize sensing-only and passive joints, ExoKit provides a module that can be mounted on top of the joint base instead of a motor (c,d). This module offers a space for an optional position encoder, hence can be repurposed as a sensing-only joint when the position encoder is attached.

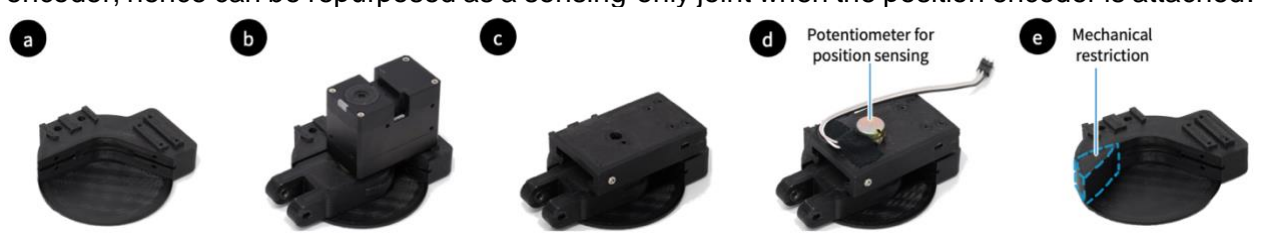
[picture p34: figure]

Mechanical restrictions for adjustability

Designers | can | add | 3d | printed | mechanical | restrictions | to | the | base | joints | (e,
restriction_20/30/45). Through a simple plug-and-play mechanism, these mechanical restrictions physically prevent the motor from exceeding the defined range of motion. They are offered in 3 different sizes (restricting the motion by 15, 30 or 45° on both sides) and can be added, removed, or exchanged after fabrication as needed.

## 3.2 Putting the Exoskeleton Together - Assembly steps

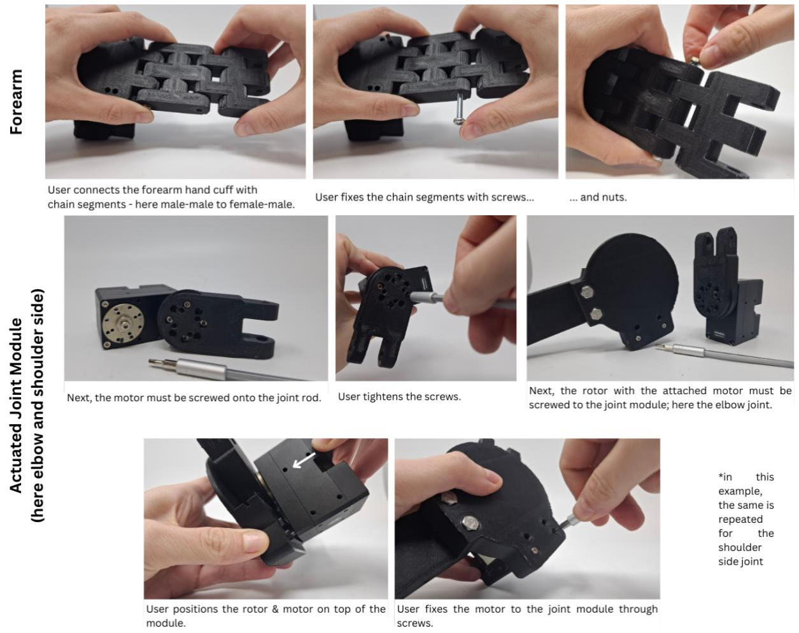
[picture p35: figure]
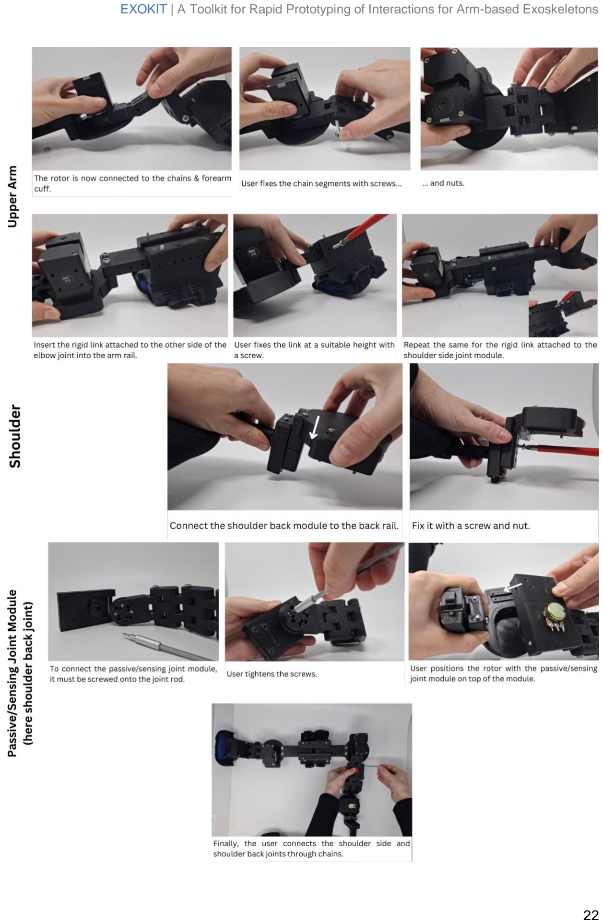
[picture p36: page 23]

## 3.3 Wiring Motors and Sensors

Connecting multiple motors

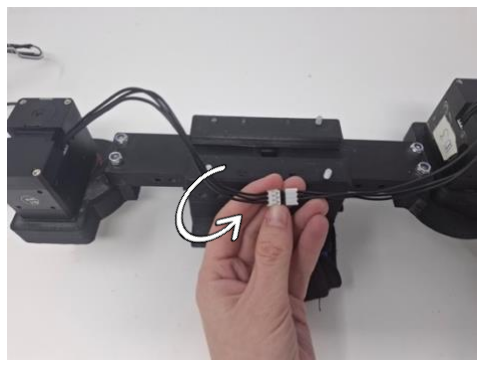
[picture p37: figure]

Connect all motors that are part of the same exoskeleton arm (up to 3 motors) to one long daisy-chain. If the cable between the two motors is too short, you can connect two shorter Dynamixel cables with each other. However, one of the two cables must be rotated by 180° before connecting them.

When connecting at least 3 motors through a daisy-chain, it is recommended to add additional power inputs. You can add a SMPS2Dynamixel adapter in between two motors and supply the adapter with extra power from the Dynamixel power supply.

Some | more | helpful | material:
https://www.youtube.com/watch?v=LN2XjlSr1kM

Connecting position encoders

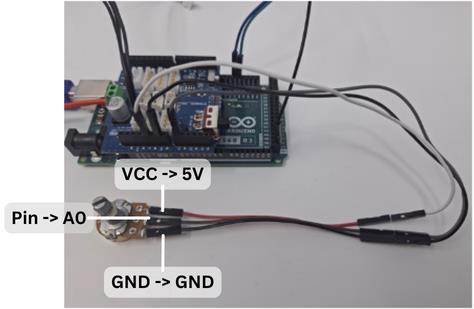
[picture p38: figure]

- Connect the VCC pin of the potentiometer to any free 5V pin on the Arduino Mega.
- Connect the analog pin of the potentiometer to any free analog pin on the Arduino Mega (e.g., A0).
- Connect the GND of the potentiometer to any free GND pin on the Arduino Mega.

Connecting the load cell

- Connect the DT and SCK pins of the HX711 module to any free analog pins on the Arduino Mega (e.g., A1 and A0)
- Connect the GND pin of the HX711 module to any free GND pin on Arduino
- Connect the VCC pin of the HX711 module to any free 5V pin on the Arduino Mega.

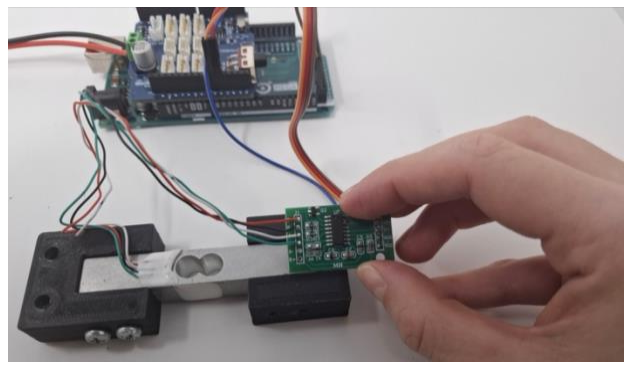
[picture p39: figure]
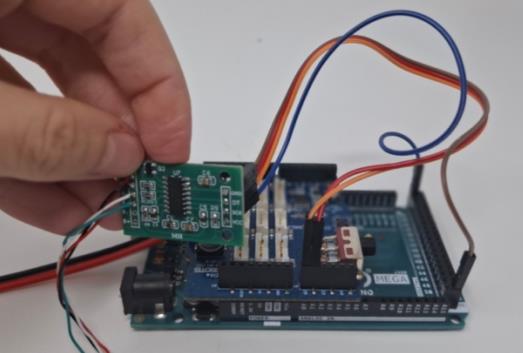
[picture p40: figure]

# 4 Using the Toolkit: Software Components

## 4.1 Overview of ExoKit’s Augmentation Strategies

ExoKit is designed to facilitate the creation of interactions for arm-based exoskeletons by providing functional abstractions that can be combined into meaningful motion interactions. These abstractions allow designers to implement both basic operations and advanced motion augmentation strategies.

💡 Exoskeletons built with ExoKit are composed of either one or two arms. Each arm consists of up to three joints ji, i ∈ {1, 2, 3}, which each can be either passive, sensing, or actuated. As a prerequisite for the following actuation functionalities, the designer must register the exoskeleton’s configuration and calibrate the absolute zero-degree position in software for each actuated or sensing joint ji once at system startup.

💡 For ease of programming, all functions are provided for controlling an individual joint only, a set of joints, or the entire arm at once.

Basic Functions

ExoKit offers various basic funtions: Moving a joint ji to an angle θi expressed as (a) absolute w.r.t. ji ’s calibrated zero-degree angle, or (b) relative to the joint’s current angle; (c) locking joint ji in place, or (d) collecting real-time sensor data of selected joints. ExoKit provides real-time sensor data about the exoskeleton’s physical angle configuration, motion velocity, acceleration, and applied torques. ExoKit can continuously stream this sensor data from selected or all joints through a serial port connection, making the data easily accessible to external applications. Functions:
- move To
- lock
- sensing

Scripted Motions

Designers can create and playback scripted sequences of motion, which are defined as a time series of basic move commands. Scripted body motions can be helpful to realize a specific repetitive motion with fixed parameters, or to play back motion sequences that serve as gestures (e.g., waving). For illustrative purposes, we provide functions for executing a waving gesture with the arm and for generating a vibrating sensation through rapid back-and-forth movements of adjustable amplitude and frequency. The latter serves as a haptic notification for the user.

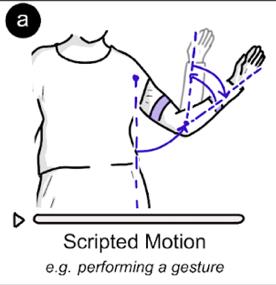
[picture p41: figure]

Functions:
- gesture
- vibration

Motion Transfer

The concept of motion transfer involves transferring human motion in real-time from one joint to another joint, from one arm to another arm, or even from one user to another person. For interaction designers, transferring motions offers flexible means for applications. These involve guiding another user’s motion, such as for motion teaching and skill transfer but also for creating shared
kinesthetic experiences between users. ExoKit offers functions that
facilitate motion transfer between two exoskeleton instances exo1

and exo2, where in every time interval, the state of the sensing joints is read and the mapped actuated joints are moved accordingly. Designers can mirror the input signal from a sensing exoskeleton arm exo1 onto an actuated counterpart exo2 and optionally scale the motion up or down by a user-defined factor f, while the system internally ensures that the scaled motion does not exceed the user’s calibrated limits of their range of motion.
Functions:
- mirror

Modulating the Motion Effort

Modulating the motion effort comprises interaction strategies in which the exoskeleton applies torques τ in or opposite to a user’s inherent motion, while preserving the user’s ability to freely navigate in space. The resulting feeling of physical assistance or resistance can be leveraged by designers to modulate how users perceive their own motion, with stronger torques τ resulting in a stronger effect. ExoKit provides two pre-implemented functions which designers can use to increase or decrease the motion effort, respectively, selectively for individual joints or applying to the entire exoskeleton. These functions include parameters that allow designers to adjust the assistive or resistive torque τ and to specify whether the strategy

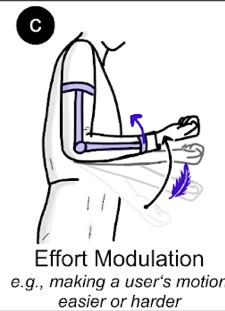
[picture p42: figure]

should be continuously active or only triggered when the user moves in a certain direction. Functions:
- amplify
- resist

Modulating the Motion Style

Modulating the motion style refers to interaction strategies that modify the observable characteristics of a user’s movement, such as speed or path, while keeping the user in control of the overall motion. These style modifications can range from subtle adjustments to more pronounced changes. ExoKit provides two pre-implemented functions to facilitate exploring modulations of motion style: (1) The exoskeleton tries to keep a user’s motion speed within a pre-defined range, by applying assistive torques τ if they are too slow or resisting ones if they are moving too fast. Designers can fine-tune these effects by setting the velocity range and the
forces applied to maintain it. (2) As an example of an artistic style modulation,
the exoskeleton can introduce jerks to augment a user’s motion path for

a more technical or robot-like motion style. A jerk consists of a short back-and-forth movement that creates a brief distortion in the user’s movement.
Functions:
- filter speed
- add jerks

Motion Guidance

ExoKit provides three complementary functions: (a) The exoskeleton can constrain the range of motion of a joint ji to an area around an absolute angle θi with range ε. As soon as the user attempts to move beyond this range, the exoskeleton tries to move the user back to the boundary with maximum torque, thereby keeping the joint within the specified limits. (b) The exoskeleton can guide the user towards an area centered around θi with range ε. Here, the exoskeleton applies assistive torques τ to ji when moving towards the desired area and resists otherwise (c) Lastly, the exoskeleton can keep a joint ji away from the area around θi, applying resistance with torque τ if the user is approaching the area and assistive torques otherwise. In addition to defining angle θi and range ε, designers can also specify the magnitude of the amplifying and resisting forces.
Functions:
- constrain to
- guide towards
- guide away

## 4.2 Overview of ExoKit’s Programming Interfaces

ExoKit provides a variety of programming interfaces designed to cater to users with different levels of expertise. By offering options for novices and advanced users, ExoKit follows a recommended practice in end-user robot programming and makes interaction programming more accessible and flexible. Below, we outline the key interfaces available.

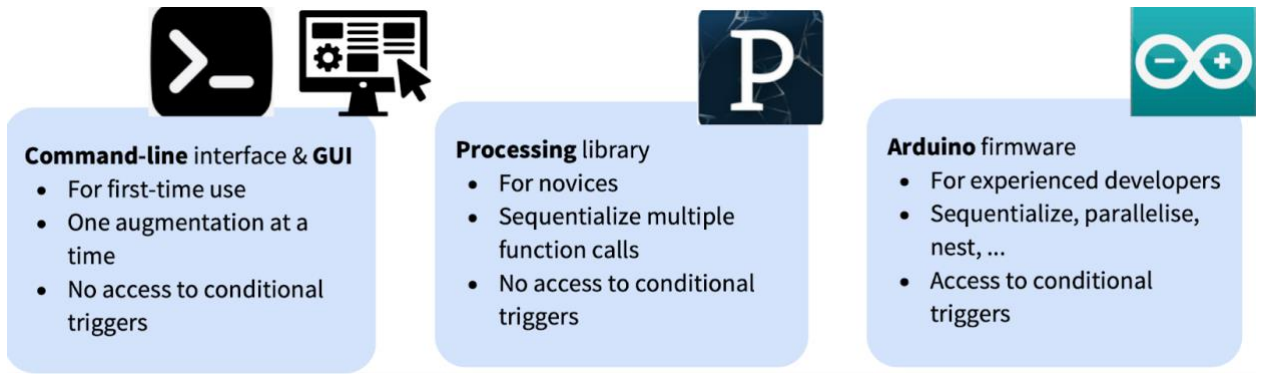
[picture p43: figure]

Command-Line Interface (CLI) & Graphical User Interface (GUI) for Novices

For users in the early stages of exploration, ExoKit offers a simple command-line interface (CLI). This interface allows the execution of basic functions and higher-level augmentation strategies while abstracting away complex programming concepts such as loops or conditional statements.

As an alternative to the terminal, novices can use a graphical user interface (GUI) programmed with Processing. The GUI enables easy execution of basic functions at the touch of a button. Sliders with labeled minimum and maximum values help guide users in selecting suitable parameters for various functions. The intuitive design of the GUI lowers the barrier for those with minimal programming experience.

Processing Library for Intermediate Users

For users looking to define sequences of motions, ExoKit provides a Processing library. This supports the creation of moderately advanced behaviors without requiring in-depth knowledge of firmware programming. It further allows to easily couple motion augmentations to graphical Processing applications.

Arduino Firmware for Advanced Users

Experienced users can directly program ExoKit's Arduino firmware to implement custom and complex behaviors. The firmware uses a trigger-action programming model built on an object-oriented, event-driven architecture. This design allows users to combine basic functions and augmentation strategies, define sequences, nested functions, and parallelized actions, and use sensor data as conditional triggers for more responsive interactions. Furthermore, users can define their own manual triggers, such that they can trigger a certain augmentation strategy when sending the self-configured command through the terminal. This allows to control the hardware also with external programs, such as with Python scripts or Processing applications.

## 4.3 Available Functions

These are the functions implemented in each of the interfaces:

| Functionality | Processing GUI | Processing Library | Arduino Library
Basic Functions | move To | ✅ | ✅ | ✅
| lock | ✅ | ✅ | ✅
| sensing | ❌ | ❌ | ✅
Scripted Motions | gesture (wave) | ✅ | ✅ | ✅
| vibration | ✅ | ✅ | ✅
Motion Transfer | mirror | ✅ | ✅ | ✅
Modulating the Motion Effort | amplify | ✅ | ✅ | ✅
| resist | ✅ | ✅ | ✅
Modulating the Motion Style | filter speed | ✅ | ✅ | ✅
| add Jerks | ✅ | ✅ | ✅
Motion Guidance | constrain To | ✅ | ✅ | ✅
| guide towards | ✅ | ✅ | ✅
| guide away | ✅ | ✅ | ✅

# 5 First Steps: Using the Processing GUI

The Processing Graphical User Interface (Processing GUI) is the recommended starting point for first-time users of ExoKit. The GUI provides a streamlined interface to access and control ExoKit’s core functionalities in a structured manner.

## 5.1 Setup

To set up ExoKit’s Processing GUI, follow these steps:

1. Prepare the Arduino Library:
- Copy the provided script (see next page) into PlatformIO.
- Replace the necessary motor Ids and pin for the emergency shutdown button in the script based on your exoskeleton configuration.
- In the provided sample script, we calibrated a left-arm exoskeleton with an active elbow joint (motor ID 3). An emergency shutdown button connected to pin 50 on the Arduino Mega. The assigned exoskeleton ID is 1.
- If you use a different exoskeleton configuration, update the code accordingly. For more details, see Chapter 7.
- Build and upload the script to the Arduino (cf., Chapter 2.4 Quick Start Guide).
- Connect to serial#2 and follow the instructions for calibration provided in the Arduino programming interface terminal.
- After calibration, disconnect the serial port in the Arduino terminal to avoid conflicts in later steps.
2. Configure the Processing GUI:
- Open the Processing GUI file.
- Identify the correct serial port (serial #2) for communication. For example:
- On Windows, the port might be COM11.
- On Linux/macOS, you can find a list of your serial devices using the command “ls /dev/tty.*“.
- Provide the correct serial port in the code:

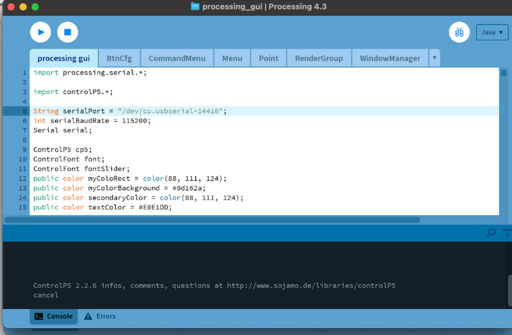
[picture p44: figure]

This is the code that must be uploaded to the Arduino programming interface:
#include <com/SerialCmdReader.h>

#include "event/simpleactionbuilder/ActionBuilder.h"

#include "exo/ConfiguredEncoder.h"

#include "DynamixelShield.h"

#include "exo/builder/ExoskeletonBuilder.h" #include "event/simpleactionbuilder/Exoskeleton.h"

DynamixelShield dxl;
ExoskeletonHandle* exoHandle;
SerialCmdReader terminalInteraction(DEBUG_SERIAL); const float DXL_PROTOCOL_VERSION = 2.0;

void setup() {
Serial.begin(1000000);
dxl.begin(1000000l);
dxl.setPortProtocolVersion(DXL_PROTOCOL_VERSION); dxl.ping(1);
DEBUG_SERIAL.begin(115200);

// TODO change the indicated Dynamixel ID (currently 3) to your Dynamixel's //ID
// TODO change the emergency button pin number or remove it if not desired exoHandle = &ExoskeletonBuilder()
.addLeftArm()
.addElbowJoint(dxl, 3, nullptr) .finishArm()
.addEmergencyShutdownButton(50,true) .build()
.calibrate(PREFER_LOAD);
exoHandle->setId(1);

terminalInteraction.enableSerialControlCommands(); }

void loop() {
taskManager.runLoop();
}

## 5.2 Usage

After launching the Processing GUI, the main interface appears (see Figure below, left). It consists of two clusters:

1. Full-Arm Functions (left cluster): Functions applied to the entire arm are accessible here.
2. Individual Joint Functions (right cluster): Functions applied to a specific joint only.

Executing Functions:

- Click on the desired function. A secondary interface will appear (see Figure below, right).
- Adjust the function’s parameters as needed:
- Specify the ID of the calibrated exoskeleton (e.g., exoID 1 in our setup).
- Select the target arm or joint for the function.
- The GUI provides default values for the other functions for convenience. Change them as you like.

A detailed explanation of the function parameters can be found in the next chapter.

- Run the function by clicking Run.
- The function will execute until you either click Cancel or execute a new function.

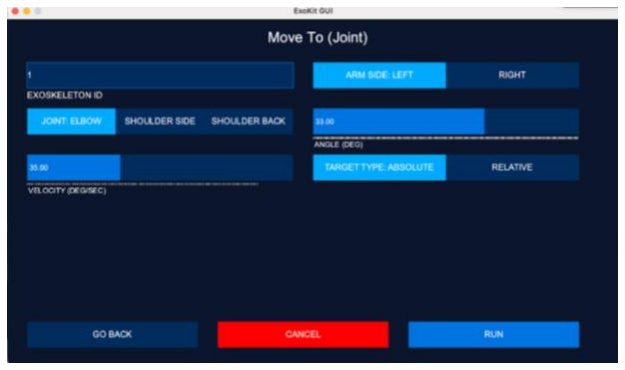
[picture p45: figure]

Tip: If you prefer command-line control, ExoKit functions can also be invoked directly using terminal commands in CLION. Refer to the Appendix for detailed instructions.

## 5.3 Troubleshooting

Here are some common issues and solutions:

Busy serial port in Processing:

- Check CLION to ensure the port is disconnected.
- Reconnect the port in Processing if necessary.

Commands do not work anymore:

- The system may have triggered an emergency shutdown. This can occur due to several reasons:
- The calibrated motion ranges were exceeded, and the system automatically performed an emergency shutdown. Reset the Arduino using the restart button and restart the Processing GUI, too.
- The motors overheated. This can happen if too much load was applied to them. Check for a blinking red light on the motor which indicative of overheating. Resolve this issue by ensuring the motors have cooled down and, resetting the Arduino using the restart button, then restarting the Processing GUI.
- Loose connections. Sometimes, this problem occurs, for instance, in case of a loose connection with the serial breakout board.

The Wave functionality does not work:

- The wave function only supports fully actuated arms. Ensure all required actuators are connected and functional.

# 6 Next Steps in Design: Implement Motion Sequences with the Processing Library

The Processing library helps users to define sequences of exoskeleton motions.

## 6.1 Setup

To leverage ExoKit’s Processing Library, follow these steps:

1. Prepare the Arduino Library (analog to Chapter 5.1):
- Copy the provided script (see next page) into PlatformIO.
- Replace the necessary motor Ids and pin for the emergency shutdown button in the script based on your exoskeleton configuration.
- In the provided sample script, we calibrated a left-arm exoskeleton with an active elbow joint (motor ID 3). An emergency shutdown button connected to pin 50 on the Arduino Mega. The assigned exoskeleton ID is 1.
- If you use a different exoskeleton configuration, update the code accordingly. For more details, see Chapter 7.
- Build and upload the script to the Arduino (cf., Chapter 2.4 Quick Start Guide).
- Connect to serial#2 and follow the instructions for calibration provided in the Arduino programming interface terminal.
- After calibration, disconnect the serial port in the Arduino terminal to avoid conflicts in later steps.

#include <com/SerialCmdReader.h>

#include "event/simpleactionbuilder/ActionBuilder.h" #include "exo/ConfiguredEncoder.h"

#include "DynamixelShield.h"

#include "exo/builder/ExoskeletonBuilder.h" #include "event/simpleactionbuilder/Exoskeleton.h"

DynamixelShield dxl;
ExoskeletonHandle* exoHandle;
SerialCmdReader terminalInteraction(DEBUG_SERIAL); const float DXL_PROTOCOL_VERSION = 2.0;

void setup() {
Serial.begin(1000000);
dxl.begin(1000000l);
dxl.setPortProtocolVersion(DXL_PROTOCOL_VERSION); dxl.ping(1);
DEBUG_SERIAL.begin(115200);
// TODO change the | indicated Dynamixel ID (currently 3) | to your
//Dynamixel's ID
// TODO change the emergency button pin number or remove it if not //desired
exoHandle = &ExoskeletonBuilder()
.addLeftArm()
.addElbowJoint(dxl, 3, nullptr) .finishArm()
.addEmergencyShutdownButton(50,true) .build()
.calibrate(PREFER_LOAD);
exoHandle->setId(1);

terminalInteraction.enableSerialControlCommands(); }

void loop() {
taskManager.runLoop();
}

2. Configure the Processing GUI:
- Open a new Processing file.
- Import the Processing library. For instance, you can simply drag-and-drop the ExoKit.jar file into the open Processing window.
- Identify the correct serial port (serial #2) for communication. For example:
- On Windows, the port might be COM11.
- On Linux/macOS, you can find a list of your serial devices using the command “ls /dev/tty.*“.
- Provide the correct serial port in the code.

Below is an example Processing code that you can use for testing:

import processing.serial.*;
int serialBaudRate = 115200;
Serial serial;

void setup() {
serial = new Serial(this, "/dev/cu.usbserial-14410", 115200);
Exokit exo = ExokitLibrary.openConnection(serial);
exo.jointMoveTo(1, | Exokit.ArmSide.LEFT, | Exokit.JointType.ELBOW, | 50, | 50,
Exokit.MoveToTargetType.ABSOLUTE);

delay(1000);
exo.jointMoveTo(1, | Exokit.ArmSide.LEFT, | Exokit.JointType.ELBOW, | -50, | 30,
Exokit.MoveToTargetType.RELATIVE);
}

void draw() {
}
First, we connect to the serial port ("/dev/cu.usbserial-14410") and then open a connection to ExoKit. Afterwards, we defined a simple motion sequence. In this example, the exoskeleton’s left elbow joint is moved to an angle of 50 degrees with a velocity of 50 degrees/second. The program then waits for one second and then sends another command. This command makes the exoskeleton’s left elbow joint move 50 degrees back with a velocity of 30 degrees/second.

## 6.2 Usage

You can use ExoKit’s Processing library to design and implement motion sequences. For the motion sequences you can use the functions which we present in the following subsections. Most functions offer two variations: Only apply to one joint, or apply to one complete arm. If default values for parameters are given, this indicates the parameter is optional.

Below, we start with an overview of parameters that almost every function uses:

int exoId | The ID of the exoskeleton as defined in the complementary Arduino script. The exoID in our provided sample scripts is always 1.
ArmSide side | The targeted arm of the exoskeleton. Options: • Exokit.ArmSide.LEFT • Exokit.ArmSide.RIGHT
JointType joint | The targeted joint of the selected arm. Options: • Exokit.JointType.ELBOW • Exokit.JointType.SHOULDER_SIDE • Exokit.JointType.SHOULDER_BACK
ExoArmAngles angles | angles is an instance of the ExoArmAngles class. It stores user-specified angles for one exoskeleton arm and comprises the targeted angle for the motors attached to the elbow, shoulder side and shoulder back.

ExoArmAngles

A new object of type ExoArmAngles can be created through
ExoArmAngles angleConfig1 = new ExoArmAngles();

The following functions are offered:
public void delElbowAngle()
public void delShoulderSideAngle() public void delShoulderBackAngle() Deletes a previously defined angle for a joint.

public void setElbowAngle(float angle) public void setShoulderSideAngle(float angle) public void setShoulderBackAngle(float angle) Sets the angle for a joint.

public float getElbowAngle()
public float getShoulderSideAngle() public float getShoulderBackAngle() Gets the angle for the joint.

public bool isHasElbow()
public bool isHasShoulderSide()

public bool isHasShoulderBack()
Checks if the angle for the joint has been defined already.

Cancel running functions

Call the following function to cancel the function that that the exoskeleton currently executes:
public void cancelRunningAction()

Basic Functions

Move To

To move an exoskeleton joint or arm to a desired position with a desired velocity, call the functions below. The motion of a joint can either be (1) absolute w.r.t. a pre-determined 0 reference-position or (2) relative to the user’s current position.

These are the signatures for the joint- and arm-based function:
public void jointMoveTo(int exoId, ArmSide side, JointType joint, float angle, float velocity, MoveToTargetType targetType);

public void armMoveTo(int exoId, ArmSide armSide, ExoArmAngles angles, float velocity);

float angle (joints) or ExoArmAngles angles (arm) | The angle(s) that the joint/arm should be moved to/by in degrees.
float velocity | The velocity that the joint(s) is moved with in degrees/second. ⚠️ Note: 0 means maximum velocity.
MoveToTargetType targetType (joints) | Determines whether the exoskeleton the exoskeleton moves by angle degrees (relative to the current position) or to the angle (absolute position w.r.t. the calibrated 0 degree angle) Options: • MoveToTargetType.ABSOLUTE • MoveToTargetType.RELATIVE ⚠️ Note: For arm motions, all motions are currently interpreted as absolute values.

Lock

Locks the user’s joint/arm in place.

These are the signatures for the joint- and arm-based function: public void jointLock(int exoId, ArmSide side, JointType joint);

public void armLock(int exoId, ArmSide side);

Scripted Motions

Gesture

Performs a pre-defined gesture.

Function Signature:
public void armGesture(int exoId, ArmSide side, Gesture gesture);

Gesture
gesture

Options:
- Exokit.Gesture.WAVE (performs a wave gesture).
- Default = Exokit.Gesture.WAVE
⚠️ Note: The waving function only works for a fully actuated exoskeleton arm!

Vibrate

Gives vibrotactile feedback.

These are the signatures for the joint- and arm-based function:
public void jointVibrate(int exoId, ArmSide side, JointType joint, int frequence, float amplitude);

public void armVibrate(int exoId, ArmSide side, int frequency, float amplitude);

int frequency | Frequency of the vibration in Hz.
float amplitude | The amplitude of the vibration in deg.

⚠️ Note: Don’t let the motors run for too long at a very high frequency as this might cause damage.

Motion Transfer

Mirror

Mirrors movements from one arm/joint (source) to another arm/joint (target) while scaling the movement by a specified factor.

These are the signatures for the joint- and arm-based function:
public void jointMirror(int targetExoId, ArmSide targetArmSide, JointType targetJoint, int sourceExoId, ArmSide sourceArmSide, JointType sourceJoint, float scaleFactor);

public void armMirror(int targetExoId, ArmSide targetArmSide, int sourceExoId, ArmSide sourceArmSide, boolean mirrorElbow, boolean mirrorShoulderSide, boolean mirrorShoulderBack, float scaleFactorElbow, float scaleFactorShoulderSide, float scaleFactorShoulderBack);

float scaleFactor (joint) | The factor by which the movement of the source gets scaled up/down when being replayed on the target. Default = 1.0
boolean mirrorElbow (arm) | Should the elbow be mirrored?
boolean mirrorShoulderSide (arm) | Should the shoulder side be mirrored?
boolean mirrorShoulderBack (arm) | Should the shoulder back be mirrored?
float scaleFactorElbow (arm) | The factor by which Elbow movements get scaled. Default = 1.0
float scaleFactorShoulderSide (arm) | The factor by which shoulder (side) movements get scaled. Default = 1.0
float scaleFactorShoulderBack (arm) | The factor by which shoulder (back) movements get scaled. Default = 1.0

⚠️ Note: Be careful with this function. Ensure there are no loose connections with the position encoder. Always test the functionality first on the table/on a mannequin before wearing it yourself. Ensure you are close to the power switch or emergency button. If there are loose connections in the position encoder, sudden peaks in the measurements can occur. As they are replayed at another joint, these sudden jerks might hurt the user.

Modulating the Motion Effort

Effort modulation comprises interaction strategies in which the exoskeleton applies forces in or opposite to a user’s inherent motion, while preserving the user’s ability to freely navigate along space. The resulting feeling of assistance or resistance can be leveraged by designers to change a user’s internal motion perception, with stronger forces resulting in a stronger effect.

Amplify

Makes it easier for the user to move.

These are the signatures for the joint- and arm-based function:

public | void | jointAmplify(int | exoId, | ArmSide | side, | JointType | joint, | float | torquePercentage,
JointMovementDirection amplifyDirection, int startingVelocity, int maxVelocity);

public void armAmplify(int exoId, ArmSide side, float torquePercentage, JointMovementDirection amplifyDirection, int startingVelocity, int maxVelocity);

float torquePercentage | Percentage (from 0 to 1) of the motor’s maximum available torque which will be used to amplify the user’s motion.
JointMovementDirect ion amplifyDirection | The exoskeleton will only amplify the motion if the user moves in the indicated direction. Options: • Exokit.JointMovementDirection.BOTH • Exokit.JointMovementDirection.ABDUCTION_OR_ FLEXION • Exokit.JointMovementDirection.ADDUCTION_EXT ENSION
int startingVelocity | The threshold velocity in deg/sec with which the user should move the joint/arm to trigger the amplification. Can be used to fine-tune the sensitivity of the function. Default = 30
int maxVelocity | The maximum velocity in deg/sec to which the function will accelerate the arm. Default = 0 ⚠️ Note: 0 means unlimited.

Resist

Makes it harder for the user to move.

These are the signatures for the joint- and arm-based function:
public | void | jointResist(int | exoId, | ArmSide | side, | JointType | joint, | float | torquePercentage,
JointMovementDirection resistDirection, float minVelocity);

public void armResist(int exoId, ArmSide side, float torquePercentage, JointMovementDirection resistDirection, int minVelocity);

float torquePercentage | Percentage (from 0 to 1) of the motor’s maximum available torque which will be used to resist the user’s motion.
JointMovementDirect ion resistDirection | The exoskeleton will only resist the motion if the user moves in the indicated direction. Options: • Exokit.JointMovementDirection.BOTH • Exokit.JointMovementDirection.ABDUCTION_OR_ FLEXION • Exokit.JointMovementDirection.ADDUCTION_EXT ENSION

| Default = Exokit.JointMovementDirection.BOTH
int minVelocity | The minimum velocity in deg/sec to which the function will slow down the arm. Default = 0

Modulating the Motion Style

Motion style refers to interaction strategies that modify the observable characteristics of a user’s movement, such as speed or path, while keeping the user in control of the overall motion. These style modifications can range from subtle adjustments to more pronounced changes.

Filter Speed

Keeps the speed of the user’s motion within a desired range. The exoskeleton will amplify the user’s motion if the user is slower than desired and resist if they are faster.

These are the signatures for the joint- and arm-based function:
public void jointFilterSpeed(int exoId, ArmSide side, JointType joint, float minSpeed float maxSpeed,
JointMovementDirection | onDirection, | float | amplifyFlexTorquePercentage, | float
resistFlexTorquePercentage, | float | amplifyExtensionTorquePercentage, | float
resistExtensionTorquePercentage);
public | void | armFilterSpeed(int | exoId, | ArmSide | side, | float | minSpeed, | float | maxSpeed,
JointMovementDirection | onDirection, | float | amplifyFlexTorquePercentage, | float
resistFlexTorquePercentage, | float | amplifyExtensionTorquePercentage, | float
resistExtensionTorquePercentage);
float minSpeed | The minimum speed in degrees/second at which the joint should move. If the joint’s speed is slower, the exoskeleton will amplify.
float maxSpeed | The maximum speed in degrees/second at which the joint should move. If the joint’s speed is faster, the exoskeleton will resist.
JointMovementDirection onDirection | The exoskeleton will only filter the speed if the user moves in the indicated direction. Options: • Exokit.JointMovementDirection.BOTH • Exokit.JointMovementDirection.ABDU CTION_OR_FLEXION • Exokit.JointMovementDirection.ADDU CTION_EXTENSION Default = Exokit.JointMovementDirection.BOTH
float amplifyFlexTorquePercentage | Percentage (from 0 to 1) of the motor’s maximum torque which will be used to amplify the motion. Will be

| applied if the joint moves too slowly and the user is doing a flexion/abduction movement. Default = 0.05
float resistFlexTorquePercentage | Percentage (from 0 to 1) of the motor’s maximum torque which will be used to provide resistance. Will be applied if the joint moves too high and the user is doing a flexion/abduction movement. Default = 0.05
float amplifyExtensionTorquePerce ntage | Percentage (from 0 to 1) of the motor’s maximum torque which will be used to amplify the motion. Will be applied if the joint moves too slowly and the user is doing an extension/adduction movement. Default = 0.05
float resistExtensionTorquePercen tage | Percentage (from 0 to 1) of the motor’s maximum torque which will be used to provide resistance. Will be applied if the joint moves too fast and the user is doing an extension/adduction movement. Default = 0.05

Jerk

Makes the user’s motion jerky: Twitches consisting of forth-and-back motions of a randomized size and within randomized time intervals will be added to the user’s motion.

These are the signatures for the joint- and arm-based function:
public void jointJerk(int exoId, ArmSide side, JointType joint, float minJerkAngle, float maxJerkAngle, int
minJerkIntervalMs, | int | maxJerkIntervalMs, | float | maxAccumulatedMovementsLeft, | float
maxAccumulatedMovementsRight, float velocity, int nrJerks);

public void armJerk(int exoId, ArmSide side, float minJerkAngle, float maxJerkAngle, int minJerkIntervalMs, int maxJerkIntervalMs, float maxAccumulatedMovementsLeft, float maxAccumulatedMovementsRight, float velocity, int nrJerks);

float minJerkAngle | The minimum size of a jerk in degrees.
float maxJerkAngle | The maximum size of a jerk in degrees.
int minJerkIntervalMs | The minimum time in between two jerks in milliseconds. ⚠️ Note: Timer runs only if joint/arm is moving

int maxJerkIntervalMs | The maximum time in between two jerks in milliseconds. ⚠️ Note: Timer runs only if joint/arm is moving
float maxAccumulatedMovementsLeft | How far should jerks be able to move the joint/arm to the left if all jerks are summed up in degrees.
float maxAccumulatedMovementsRight | How far should jerks be able to move the joint/arm to the right if all jerks are summed up in degrees.
float velocity | The velocity of the jerks in deg/sec. Default = 0.0 ⚠️ Note: 0 means unlimited.
int nrJerks | The number of jerks that will be performed. Default = 0 ⚠️ Note: 0 means unlimited.

⚠️ Note: Jerks only occur if the arm is in motion.

Motion Guidance

Motion guidance comprises strategies in which the exoskeleton applies forces that correct, guide, or constrain a user’s movement. As the forces increase and the unconstrained range of motion decreases, the user’s motion becomes more controlled, up to being fully moved or locked. Conversely, weaker forces and larger unconstrained areas allow the user to move more

freely.

Constrain To

Restricts a user’s motion range to a specified area. The area is determined by a range ε (here called radius) around a center angle θ.

These are the signatures for the joint- and arm-based function:
public void jointConstrainTo(int exoId, ArmSide side, JointType joint, float angle, float radius);

public void armConstrainTo(int exoId, ArmSide side, ExoArmAngles angles, float radius);

float angle (joint)
or
ExoArmAngles angles (arms)

The center of the area in degree.

float radius | The radius around the center angle in degrees.

Guide Away

Guides a user’s away from a specified area. The area is determined by a range ε (here called radius) around a center angle θ. The user cannot enter the area at all.

These are the signatures for the joint- and arm-based function:
public void jointGuideAway(int exoId, ArmSide side, JointType joint, float angle, float radius, float amplifyTorquePercentage, float resistTorquePercentage);

public void armGuideAway(int exoId, ArmSide side, ExoArmAngles angles, float radius, float amplifyTorquePercentage, float resistTorquePercentage);

float angle (joint) or ExoArmAngles angles(arms) | The center of the area in degree.
float radius | The radius around the center angle in degrees.
float amplifyTorquePercentage | Percentage (from 0 to 1) of the motor’s maximum torque which will be used to amplify the motion. Will be applied if the joint moves away from the forbidden area. Default = 0.05
float resistTorquePercentage | Percentage (from 0 to 1) of the motor’s maximum torque which will be used to resist the motion. Will be applied if the joint moves towards the forbidden area. Default = 0.05

Guide Towards

Guides a user towards a specified area. The area is determined by a range ε (here called radius) around a center angle θ. Within the area, the user can freely move.

These are the signatures for the joint- and arm-based function:
public void jointGuideTowards(int exoId, ArmSide side, JointType joint, float angle, float radius, float amplifyTorquePercentage, float resistTorquePercentage);

public void armGuideTowards(int exoId, ArmSide side, ExoArmAngles armAngles, float radius, float amplifyTorquePercentage, float resistTorquePercentage);

float angle (joint)
or

The center of the area in degree.

ExoArmAngles angles(arms)

float radius | The radius around the center angle in degrees.
float amplifyTorquePercentage | Percentage (from 0 to 1) of the motor’s maximum torque which will be used to amplify the motion. Will be applied if the joint moves towards the desired area. Default = 0.05
float resistTorquePercentage | Percentage (from 0 to 1) of the motor’s maximum torque which will be used to resist the motion. Will be applied if the joint moves away from the desired area. Default = 0.05

## 6.3 Troubleshooting

Here are some common issues and solutions:

Busy serial port in Processing:

- Check CLION to ensure the port is disconnected.
- Reconnect the port in Processing if necessary.

Commands do not work anymore:

- The system may have triggered an emergency shutdown. This can occur due to several reasons:
- The calibrated motion ranges were exceeded, and the system automatically performed an emergency shutdown. Reset the Arduino using the restart button and restart the Processing GUI, too.
- The motors overheated. This can happen if too much load was applied to them. Check for a blinking red light on the motor which indicative of overheating. Resolve this issue by ensuring the motors have cooled down and, resetting the Arduino using the restart button, then restarting the Processing GUI.
- Loose connections. Sometimes, this problem occurs, for instance, in case of a loose connection with the serial breakout board.

The Wave functionality does not work:

- The wave function only supports fully actuated arms. Ensure all required actuators are connected and functional.

7 Deep | Dive: | Implementing | Complex

# Interactions with the Arduino Library

The Arduino programming interface is recommended for more advanced users that are familiar with the working principles of the pre-implemented functionalities and/or want to define more interactive behavior. To provide a powerful interface, it relies on ist own control structure on which we detail in this chapter:

## 7.1 Core Structure

The following code provides a scaffold to initialize libraries that ExoKit depends on. This is the main.cpp of a standard Arduino script using ExoKit:

// main.cpp

#include "TaskManagerIO.h" #include "util/DebugSerial.h" #include "com/SerialCmdReader.h" #include "DynamixelShield.h"

const float DXL_PROTOCOL_VERSION = 2.0; SerialCmdReader cmdReader(DEBUG_SERIAL); DynamixelShield dxl;

void setup() {
dxl.begin(1000000l);
dxl.setPortProtocolVersion(DXL_PROTOCOL_VERSION); dxl.ping(1);

DEBUG_SERIAL.begin(115200);

// <EXOSKELETON CONFIGURATION & CALIBRATION (CHAPTER 7.2)> // <CONDITION-ACTION PROGRAMMING (CHAPTER 7.3)>
}

void loop() {
taskManager.runLoop();
}

setup()-function

The setup function is the function in which you will define most of the exoskeleton's interactive behavior.
Before doing this, we first must setup up the communication with the motors and the PC. In order to be able to use Dynamixel servos, the Dynamixel shields needs to be set up, which includes setting the baudrate for the communication between the motors and the microcontroller. The

Arduino Mega can communicate with the servos using a bauddrate of up to 1.000.000 bd. Next we enable the DEBUG_SERIAL console, which is used to exchange information between a PC and the exoskeleton. It communicates over Serial #2 (Pin 16 and 17) on an Arduino Mega. Afterwards follows the code with which the physical exoskeleton setup will be registered and calibrated (see Chapter 7.2). Then the interactive behavior will be programmed (see Chapter 7.3).

loop()-function

ExoKit runs all actions and conditions using tasks that are managed by TaskManagerIO and registered in the setup() function. For this reason, the only method called in the loop()-function is taskManager.runLoop(), which schedules and executes ExoKits functions.

## 7.2 Exoskeleton Configuration and Calibration

#include <com/SerialCmdReader.h>

#include "event/simpleactionbuilder/ActionBuilder.h" #include "exo/ConfiguredEncoder.h"

#include "DynamixelShield.h"

#include "exo/builder/ExoskeletonBuilder.h" #include "event/simpleactionbuilder/Exoskeleton.h"

DynamixelShield dxl;
ExoskeletonHandle* exoHandle;
Exoskeleton* exoskeleton;
ActionBuilder ab;
const float DXL_PROTOCOL_VERSION = 2.0; ExoArmAngles angleConfig1;

void setup() {
Serial.begin(1000000);
dxl.begin(1000000l);
dxl.setPortProtocolVersion(DXL_PROTOCOL_VERSION); dxl.ping(1);

DEBUG_SERIAL.begin(115200);

exoHandle = &ExoskeletonBuilder()
.addLeftArm() | // returns an ArmBuilder& object
.addElbowJoint(dxl, 1, nullptr) // returns an ArmBuilder& object .addShoulderSideJoint(dxl, 2, nullptr) .addShoulderBackJoint(dxl, 3, nullptr)
.finishArm() | // returns an ExoBuilder& object
.addEmergencyShutdownButton(50,true)// returns an ExoBuilder& object
.build() | // returns an ExoskeletonCalibrator& object
.calibrate(PREFER_LOAD); | // returns an ExoskeletonHandle& object

exoskeleton = new Exoskeleton{ab, *exoHandle}; // create the exoskeleton

// <CONDITION-ACTION PROGRAMMING (CHAPTER 7.3)>
}

void loop() {
taskManager.runLoop();
}

The code snipped above shows an example on how to configure an exoskeleton instance. It comprises one left arm with three active joints and an emergency shutdown button.

For an example of how to configure an exoskeleton with a load cell or a position encoder, see the example scripts in Appendix B and C.

The following methods are available for configuring the exoskeleton:

ExoskeletonBuilder

ArmBuilder& ExoskeletonBuilder::addLeftArm();

ArmBuilder& ExoskeletonBuilder::addRightArm(); Starts the configuration of the selected arm.

ExoskeletonBuilder&
ExoskeletonBuilder::addEmergencyShutdownButton(uint8_t buttonPin, bool isPullUp);
Configures the emergency shutdown button. If the corresponding button is pressed, the exoskeleton disables all configured motors and shuts down.

ExoskeletonCalibrator ExoskeletonBuilder::build(); Completes the configuration step. It returns an ExoskeletonCalibrator object.

ArmBuilder

Given an ArmBuilder object, joints can be added to the arm. To add an active joint (a joint with a motor) to the arm, use the following function:
ArmBuilder& | ArmBuilder::addElbowJoint(DynamixelShield& | dxl, | uint8_t
dxl_id, HX711* loadCell = nullptr, uint8_t lower_mechanical_restriction = 0, uint8_t upper_mechanical_restriction = 0);
ArmBuilder& | ArmBuilder::addShoulderSideJoint(DynamixelShield& | dxl,
uint8_t | dxl_id, | HX711* | loadCell | = | nullptr, | uint8_t
lower_mechanical_restriction = 0, uint8_t upper_mechanical_restriction = 0);
ArmBuilder& | ArmBuilder::addShoulderBackJoint(DynamixelShield& | dxl,
uint8_t | dxl_id, | HX711* | loadCell | = | nullptr, | uint8_t
lower_mechanical_restriction = 0, uint8_t upper_mechanical_restriction = 0);
DynamixelShield& dxl | A pointer to the the instance of the Dynamixel shield to which the motors are attached.
uint8_t dxl_id | The ID motor attached to the joint module.
HX711* loadCell | A loadcell object. Default = nullptr
uint8_t lower_mechanical_restriction | The degree (positive) by which the joint’s range of motion has been reduced at the lower end of the joint module through a mechanical restriction. Default = 0
uint8_t upper_mechanical_restriction | The degree (positive) by which the joint’s range of motion has been reduced at the lower end of the joint module through a mechanical restriction.

Default = 0

To add a passive joint (either without any sensor and actuator or with a position encoder), use the following functions:
ArmBuilder& | ArmBuilder::addElbowJoint(ConfiguredEncoder* | encoder | =
nullptr, HX711* loadCell = nullptr, uint8_t lower_mechanical_restriction = 0, uint8_t upper_mechanical_restriction = 0);

ArmBuilder& ArmBuilder::addShoulderSideJoint(ConfiguredEncoder* encoder
= | nullptr, | HX711* | loadCell | = | nullptr, | uint8_t
lower_mechanical_restriction = 0, uint8_t upper_mechanical_restriction = 0);

ArmBuilder& ArmBuilder::addShoulderBackJoint(ConfiguredEncoder* encoder
= | nullptr, | HX711* | loadCell | = | nullptr, | uint8_t
lower_mechanical_restriction = 0, uint8_t upper_mechanical_restriction = 0);

Configures the elbow joint as a passive joint. All parameters are optional.

ConfiguredEncoder* encoder | A potentiometer object that is used to read the joint’s position and velocity. Default = nullptr
HX711* loadCell | A loadcell object. Default = nullptr
uint8_t lower_mechanical_restriction | The degree (positive) by which the joint’s range of motion has been reduced at the lower end of the joint module through a mechanical restriction. Default = 0
uint8_t upper_mechanical_restriction | The degree (positive) by which the joint’s range of motion has been reduced at the lower end of the joint module through a mechanical restriction. Default = 0

To complete the configuration process of the current arm, call:

ExoskeletonBuilder& ArmBuilder::finishArm();

ExoskeletonCalibrator

The calibrate-method starts the calibration of the exoskeleton and returns an ExoskeletonHandle. During the calibration the 0-degree positions of all joints are configured and persisted in the Arduino’s EEPROM.
The DEBUG_SERIAL console is used to guide the user through the calibration process.

ExoskeletonHandle& calibrate(ConfigLoadBehaviour configLoadBehaviour = ASK_CREATE);
There are three different options for the calibration process:
ConfigLoadBehaviour.CREATE | Triggers a calibration after each restart of the Arduino. It does not ask the user if they want to persist the created calibration. Hence, this mode always requires interaction through the serial console and is not suited for mobile usage in which the Arduino is not connected to the PC’s serial port.
ConfigLoadBehaviour.ASK_CREATE | If the Arduino is restarted, the system asks if the user wants to perform a new calibration of the exoskeleton, or if the persisted calibration parameters should be applied. As the previous mode, it requires interaction with the serial console.
ConfigLoadBehaviour.PREFER_LOAD | Automatically loads the persisted calibration parameters from the EEPROM. If the persisted parameters were determined for a different configuration, the system asks the user to perform a new calibration. This mode does not require no interaction with the serial console if configured once for the correct exoskeleton configuration. Hence, this mode should be used for a mobile setup.

## 7.3 Defining the Program Flow With Condition-Action Programming

ExoKit follows an event-based architecture, in which interactive behavior is modeled with Condition and Action classes (see Chapters 7.4 and 7.5). Conditions serve as runtime triggers that control the flow of actions, evaluating to true or false based on the exoskeleton’s current state. This evaluation is checked in a control loop that runs at a fixed frequency. Actions encapsulate basic functions and augmentation strategies (see prior Chapters). ExoKit allows to combine the actions sequentially or in parallel either for individual joints, a set of joints, or the arm for complex control flows.

The latter is achieved with the help of two classes: ActionBuilder and Exoskeleton.

After the desired condition-action sequences are defined, they need to be dispatched, using the ActionBuilders dispatch function:
ActionBuilder::dispatch(ICondition& | condition, | unsigned | long
loopInterval, boolean multipleTrigger)
ICondition& condition | The dispatch function receives a condition. The dispatched sequence is triggered if the condition evaluates to true.
unsigned long loopInterval | Defines the frequency in milliseconds in which the task that runs the action sequence will be called. A smaller number means that the exoskeleton reacts faster to changes as it checkst he condition more often.
boolean multipleTrigger | After the dispatched function has finished, this parameter decides whether the function can be triggered again if the condition evaluates to true. If false, then once the function was triggered, it won’t be executed again even if the condition would evaluate to true.

An example scaffold:
#include | <com/SerialCmdReader.h>

#include | "event/simpleactionbuilder/ActionBuilder.h"

#include | "exo/ConfiguredEncoder.h"

#include | "DynamixelShield.h"

#include | "exo/builder/ExoskeletonBuilder.h"

#include | "event/simpleactionbuilder/Exoskeleton.h"

DynamixelShield | | | | | | dxl;
ExoskeletonHandle* | exoHandle;
Exoskeleton* exoskeleton; | // | create | a | global | Exoskeleton | object
ActionBuilder ab; | // create a global ActionBuilder object
const | float | DXL_PROTOCOL_VERSION | = | 2.0;
void | | setup() | | | | {
Serial.begin(1000000);
dxl.begin(1000000l);

dxl.setPortProtocolVersion(DXL_PROTOCOL_VERSION); dxl.ping(1);

DEBUG_SERIAL.begin(115200);

// <EXOSKELETON CONFIGURATION & CALIBRATION (CHAPTER 7.2)>

exoskeleton = new Exoskeleton{ab, *exoHandle}; // initialize the
| | exoskeleton | object
// <CONDITION-ACTION PROGRAMMING (CHAPTER 7.3)>

ab.dispatch(ab.trueCondition(), 80); // the sequence is immediately executed. It runs at a frequency
of | 80 | milliseconds
}
void | | loop() | {
taskManager.runLoop();
}

Sequential execution of actions

Sequences are programmed the same way as one would write a normal program. The classes ActionBuilder and Exoskeleton provide various methods can be used to program the exoskeletons behaviour.
Calling one behaviour defining method `A` first and another method `B` second, means that the behaviour defined by `B` executes after `A` finished.

Example:
Exoskeleton->getLeftArm().getElbow().resist(0.05, ExoskeletonJointHandle::BOTH,0, ab.timeoutCondition(5000));

ab.delay(5000);

exoskeleton->getLeftArm().getElbow().amplify(0.05, ExoskeletonJointHandle::BOTH);

The code above first lets the exoskeleton resist elbow movements for 5 seconds, then does nothing for 5 seconds and amplifies elbow movements afterwards.

Parallel execution of actions

The parallel block makes the exoskeleton execute two functions in parallel, which is for example useful if two different joints should perform two different functions at the same time.
The parallel block finishes if both actions defined in the two parallel functions are finished.
void | parallel(void | (*firstParallel)(ActionBuilder&), | void
(*secondParallel)(ActionBuilder&));

Example:
void firstParallelBlock(ActionBuilder& ab) {

exoskeleton->getLeftArm().getShoulderSide().moveToActive(60, 20); }

void secondParallelBlock(ActionBuilder& ab) { exoskeleton->getLeftArm().getElbow().moveToActive(30, 20); }

void setup() {
<SETUP/CONFIGURATION/CALIBRATION>

ab.parallel(firstParallelBlock, secondParallelBlock); ab.dispatch(ab.trueCondition(), 1, true);
}

If-then-else

The ifThenElse block takes a condition and two functions defining the then and else blocks. If the condition evaluates to true, the sequential behaviour that is defined in the thenBlock function is executed. Otherwise the behaviour defined in the elseBlock function is executed.
void | ifThenElse(ICondition& | condition, | void
(*thenBlock)(ActionBuilder&), void (*elseBlock)(ActionBuilder&));

Example:
void thenBlock(ActionBuilder& ab) { exoskeleton->getLeftArm().getElbow().moveToActive(60, 20); }

void elseBlock(ActionBuilder& ab) { exoskeleton->getLeftArm().getElbow().moveToActive(30, 20); }

void setup() {
<SETUP/CONFIGURATION/CALIBRATION>

ab.ifThenElse(ab.trueCondition(), thenBlock, elseBlock); ab.dispatch(ab.trueCondition(), 1, true);
}

Loop

The loop block corresponds to a while call. It takes a loopCondition and one function, the inLoopBlock, comprising a sequence of actions that corresponds to the body of the loop. If the loopCondition evaluates to true, the actions defined in the inLoopBlock are executed. Just like a while block, this loop block checks the loopCondition again after the code in the inLoopBlock-function finishes. If the condition evaluates to false, the loop block finishes.
void | loop(ICondition& | loopCondition, | void
(*inLoopBlock)(ActionBuilder&));

Example:
void loopBlock(ActionBuilder& ab) { exoskeleton->getLeftArm().getElbow().moveToActive(30, 20); exoskeleton->getLeftArm().getElbow().moveToActive(60, 20); }

void setup() {
<SETUP/CONFIGURATION/CALIBRATION>

ab.loop(ab.trueCondition(), loopBlock); ab.dispatch(ab.trueCondition(), 1, true);
}

The code above would let the exoskeleton move the user's elbow up and down in a never ending loop.

Breakable

The breakable block continuously evaluates the breakIf condition while executing the actions defined in the block-function. If the breakIf condition evaluates to true, the in the block-function defined action gets aborted mid run.
void | breakableBlock(ICondition& | breakIf, | void
(*block)(ActionBuilder&));

Important function calls and classes

As in the Processing library, indicating the ExoID, targeted arm side of the exoskeleton as well as the joint are important for telling the API where it should execute an action and monitor conditions.

Getting the arm and joint objects

Getting the arm and joint objects is important for defining conditions and actions. The ExoskeletonArm object contains all actions that can be performed directly on an arm. The ExoskeletonJoint object contains all actions and conditions that can be performed or evaluated on a joint.
To get these objects, you can use the following functions:

ExoskeletonArm &Exoskeleton::getLeftArm() Gets the left arm of an exoskeleton.

ExoskeletonArm &Exoskeleton::getRightArm() Gets the right arm on an exoskeleton.

ExoskeletonJoint& ExoskeletonArm::getElbow();
Gets the elbow joint from an arm.

ExoskeletonJoint& ExoskeletonArm::getShoulderBack(); Gets the shoulder back joint of an arm.

ExoskeletonJoint& ExoskeletonArm::getShoulderSide(); Gets the shoulder side joint of an arm.

ExoArmAngles

As in the Processing library, ExoArmAngles is a class that helps the user store the goal angles for an exoskeleton arm.

Here methods for the elbow joints are getting explained, but methods for ShoulderSide and ShoulderBack work the same:

void ExoArmAngles::setElbowAngle(float angle)
Sets the angle for the elbow.

float ExoArmAngles::getElbowAngle()
Gets the angle for the elbow.

bool ExoArmAngles::isHasElbow() Checks if the angle for the elbow has been defined.

void ExoArmAngles::delElbowAngle() Deletes a previously defined angle for the elbow.

Example:
#include <com/SerialCmdReader.h>

#include "event/simpleactionbuilder/ActionBuilder.h" #include "exo/ConfiguredEncoder.h"

#include "DynamixelShield.h"

#include "exo/builder/ExoskeletonBuilder.h" #include "event/simpleactionbuilder/Exoskeleton.h"

DynamixelShield dxl;
ExoskeletonHandle* exoHandle;
Exoskeleton* exoskeleton;
ActionBuilder ab;
const float DXL_PROTOCOL_VERSION = 2.0; ExoArmAngles angleConfig1;

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

// TODO change the indicated Dynamixel ID (currently 1, 2, ,3) to your Dynamixel's ID
exoHandle = &ExoskeletonBuilder()
.addLeftArm()
.addElbowJoint(dxl, 1, nullptr) .addShoulderSideJoint(dxl, 2, nullptr) .addShoulderBackJoint(dxl, 3, nullptr) .finishArm()
.addEmergencyShutdownButton(50,true) .build()
.calibrate(PREFER_LOAD);
exoskeleton = new Exoskeleton{ab, *exoHandle};

angleConfig1.setElbowAngle(10); angleConfig1.setShoulderSideAngle(10); angleConfig1.setShoulderBackAngle(10); exoskeleton->getLeftArm().moveTo(angleConfig1,20, nullptr);

ab.dispatch(ab.trueCondition(), 80);
}

void loop() {
taskManager.runLoop();
}

## 7.4 Conditions

Conditions are used for various purposes within ExoKit‘s API. For example, they can be used to trigger an action sequence, to end the execution of an action or as deciders for control flow blocks. Conditions evaluate at runtime and return boolean values “True” or “False”. They can be composed using boolean operations.

Conditions that observe a joint or an arm can be generated using the ExoskeletonJoint object. Example:
exoskeleton->getLeftArm().getElbow().isAtPosition(/* ..*/);
The code above generates a condition that checks if the motor at the left elbow is at a specific position.

Conditions that are not related to a specific joint or arm are generated using the ActionBuilder object. Example:
ab.trueCondition()
The above example always evaluates to true.

To compose conditions, the boolean operators “!”, “||” and “&&” are used directly in the code. Example:
ICondition& | c | = | exoskeleton->getLeftArm().getElbow().isAtPosition(/*
..*/) && !exoskeleton->getLeftArm().getElbow().isMoving();
The above example evaluates to true if the elbow is at a specific position and is not moving.

true

Always evaluates to true.
ICondition& ActionBuilder::trueCondition();

false

Always evaluates to false.
ICondition& ActionBuilder::falseCondition();

timeout

After being checked for the first time, the condition starts a timer. It evaluates to true after the timer expires. The conditions resets when the action finishes. The same instance can be used for multiple actions/triggers.
ICondition& ActionBuilder::timeoutCondition(unsigned long wait_ms);

unsigned long wait_ms The time which the condition should wait in milliseconds.

manualCondition

A condition that can be set manually either through custom code or by using a custom command that can be sent through the serial console. The latter is useful to trigger actions through an external application that sends out user-defined commands through the serial port. To use this condition, create an instance of ManualConditionTriggerCmd with a command name and the condition as a parameter and an instance of SerialCmdReader. Register the manual condition trigger using the add-function of your instance of the SerialCmdReader .
ICondition& | ActionBuilder::manualCondition(bool | unfulfillOnRestore | =
true, bool armOnFirstEval = false);
bool unfulfillOnRestore | Determines if the condition should be set back to false if the action it triggered has finished.
bool armOnFirstEval | Determines if the condition should ignore it being set to ‘true’ if the action it was assigned to didn’t evaluate it yet. An action evaluates a condition at its start and continuously while it runs.

isVelocity

Compares the velocity of a joint to a user-defined threshold or range.
VelocityCondition& | ExoskeletonJoint::isVelocity(SpeedCompareType
compare, float degreePerSecond, float tolerance = 0)
SpeedCompareType compare | The compare operation that is used. The measured sensor data of the joint is always on the left side of the operation and the threshold degreePerSecond is always on the right side. Options: • FASTER_THAN • SLOWER_THAN • WITHIN E.g., the function reads as ‘the current velocity of the joint is FASTER_THAN the user-specified threshold degreePerSecond’
float degreePerSecond | The value to compare the joint’s velocity with in degrees/second. If compare == WITHIN, this value indicates the center of the range in which the condition should evaluate to true.
float tolerance | The tolerance for degreePerSecond in degrees/second. If compare == WITHIN, this defines the size of the range around the center in which the condition should evaluate to true. Default = 0

isSpeed

Compares the speed of a joint to a user-defined threshold or range.
SpeedCondition& ExoskeletonJoint::isSpeed(SpeedCompareType compareType, float thresholdDegreePerSecond, float tolerance = 0);
SpeedCompareType compare | The compare operation that is used. The measured sensor data of the joint is always on the left side of the operation and the threshold degreePerSecond is always on the right side. Options: • FASTER_THAN • SLOWER_THAN • WITHIN
float degreePerSecond | The value to compare the joint’s velocity with in degrees/second. If compare == WITHIN, this value indicates the center of the range in which the condition should evaluate to true.
float tolerance | The tolerance for degreePerSecond in degrees/second. If compare == WITHIN, this defines the size of the range around the center in which the condition should evaluate to true. Default = 0

isMovingTowards

Evaluates to true if a joint is moving towards the specified direction.
IsMovingTowardCondition&
ExoskeletonJoint::isMovingTowards(ExoskeletonJointHandle::MovementDire ction direction, float thresholdVelocity = 5);
ExoskeletonJointHandle::Mo vementDirection direction | The movement direction that the condition should observe. Options: • ExoskeletonJointHandle::MovementDirect ion.BOTH • ExoskeletonJointHandle::MovementDirect ion.ABDUCTION_OR_FLEXION • ExoskeletonJointHandle::MovementDirect ion.ADDUCTION_EXTENSION
float thresholdVelocity | How fast the joint needs to move at a minimum in degrees/second to be considered as moving. Default = 5

isMoving

Evaluates to true if the joint is moving with a speed greater than 0 deg/sec.

IsMovingCondition& ExoskeletonJoint::isMoving();

isAcceleration

Compares the acceleration of a joint to a user-defined threshold or range.
AccelerationCondition&
ExoskeletonJoint::isAcceleration(SpeedCompareType | compareType, | float
accleration, float tolerance = 0);
SpeedCompareType compare | The compare operation that is used. The value of the joint is always on the left side of the operation and thresholdDegreePerSecond is always on the right side. Options: • FASTER_THAN • SLOWER_THAN • WITHIN
float acceleration | The value to compare the joint’s velocity with in degrees/second². If compare == WITHIN, this value indicates the center of the range in which the condition should evaluate to true.
float tolerance | The tolerance for acceleration in degrees/second². If compare == WITHIN, this defines the size of the range around the center in which the condition should evaluate to true. Default = 0

isAccelerating

Evaluates to true if the joint’s speed is increasing.
IsAcceleratingCondition& | ExoskeletonJoint::isAccelerating(float
accelerationThreshold = 1);

float
accelerationThreshold

How much the joint needs to accelerate at a minimum in degrees/second² to be considered as accelerating. Default = 1

isForce

Compares the force measurement of a load cell registered with this joint to a user-defined threshold or range.
ForceCondition&
ExoskeletonJoint::isForce(ForceCondition::ForceCompareType compareType, float force, float tolerance = 0);

ForceCondition::
ForceCompareType
compareType

Options:
- STRONGER_THAN
- WEAKER_THAN

| • WITHIN
float force | The value to compare the applied force. If compare == WITHIN, this value indicates the center of the range in which the condition should evaluate to true.
float tolerance | The tolerance for force. If compare == WITHIN, this defines the size of the range around the center in which the condition should evaluate to true. Default = 0

isAtPosition

Evaluates to true if the joint is in the position of the specified angle
AtPositionCondition& | ExoskeletonJoint::isAtPosition(CompareType
compareType, float angle, float tolerance);
CompareType compareType | Options: • EQUAL • LOWER_THAN • HIGHER_EQUAL_THAN
float angle | The absolute angle in degrees to compare to.
float tolerance | The tolerance range in degrees around the goal angle in which the joint should still being considered to be in the position.

isAtExoArmAngle

Evaluates to true if all arm joints capable of tracking are in the desired position for a specific duration. This can be used for pose detection.
ICondition& | ExoskeletonArm::isAtExoArmAngle(ExoArmAngles | exoArmAngle,
float tolerance, unsigned long duration);
ExoArmAngles exoArmAngle | The angles of the arm.
float tolerance | The tolerance range in degrees around the goal angle in which the joint should still being considered to be in the position.
unsigned long duration | How long the users needs to stay in the position before the conditions evaluates to true in milliseconds.
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

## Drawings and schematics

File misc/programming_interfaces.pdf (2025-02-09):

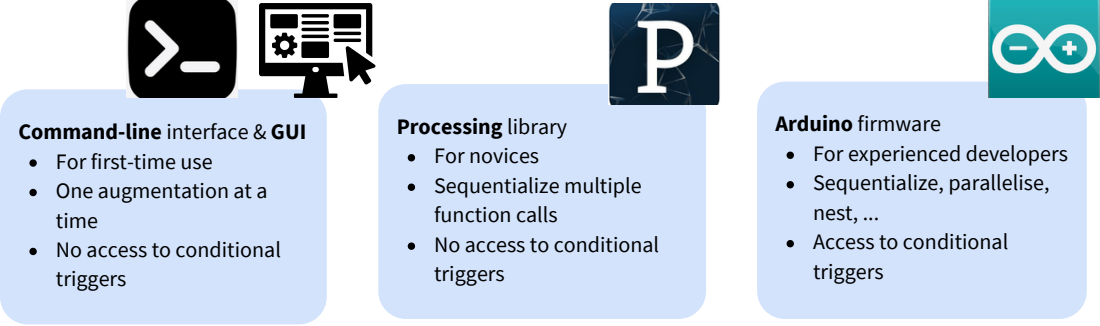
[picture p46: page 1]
lib; vic; tia; liz; tip; tio; ditio; rig; fir; tim; rie; lis; , ... Access t

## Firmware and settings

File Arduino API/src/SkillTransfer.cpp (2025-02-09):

//
// Created by Alexander on 03.09.2024.
//
/*
#include "event/simpleactionbuilder/ActionBuilder.h"
#include "exo/ConfiguredEncoder.h"
#include "DynamixelShield.h"
#include "exo/builder/ExoskeletonBuilder.h"
#include "event/simpleactionbuilder/Exoskeleton.h"

DynamixelShield dxl;
ExoskeletonHandle* exoHandle;
ConfiguredEncoder encoderElbow(A2, 300);
ConfiguredEncoder eEncoderShoulderBack(A0, 300);
ConfiguredEncoder encoderShoulderSide(A1, 300);
ActionBuilder ab;
Exoskeleton* exoskeleton; 
const float DXL_PROTOCOL_VERSION = 2.0;


void mirrorElbow2ShoulderSide(ActionBuilder& ab) {
    exoskeleton->getLeftArm().getShoulderSide().mirror(exoHandle->getRightArm().getElbow(), 1, nullptr);
}

void mirrorShoulderSide2Elbow(ActionBuilder& ab) {
    exoskeleton->getLeftArm().getElbow().mirror(exoHandle->getRightArm().getShoulderSide(), 1, nullptr);
}

void mirrorShoulderBack(ActionBuilder& ab)
{
    exoskeleton->getLeftArm().getShoulderBack().mirror(exoHandle->getRightArm().getShoulderBack(), 1, nullptr);
}
void mirrorOtherJoints(ActionBuilder& ab)
{
    ab.parallel(mirrorShoulderSide2Elbow,mirrorShoulderBack);
}

void setup() {
    Serial.begin(1000000);

    dxl.begin(1000000l);
    dxl.setPortProtocolVersion(DXL_PROTOCOL_VERSION);
    dxl.ping(1);

    DEBUG_SERIAL.begin(115200);

    exoHandle = &ExoskeletonBuilder()
            .addLeftArm()
            .addElbowJoint(dxl, 4, nullptr)
            .addShoulderSideJoint(dxl, 1, nullptr)
            .addShoulderBackJoint(dxl, 2, nullptr)
            .finishArm()
            .addRightArm()
            .addElbowJoint(&encoderElbow, nullptr)
            .addShoulderSideJoint(&encoderShoulderSide, nullptr)
            .addShoulderBackJoint(&eEncoderShoulderBack, nullptr)
            .finishArm()
            .build()
            .calibrate(ASK_CREATE);

    exoskeleton = new Exoskeleton{ab, *exoHandle};
    // collaborative body-actuated play - level 1
    //exoskeleton->getLeftArm().mirror(exo->getRightArm(), true, true, true);

    // collaborative body-actuated play - level 2
    //exoskeleton->getLeftArm().mirror(exo->getRightArm(), true, true, true, 2, 2, 2);

    // collaborative body-actuated play - level 3
    ab.parallel(mirrorElbow2ShoulderSide, mirrorOtherJoints);

    ab.dispatch(ab.trueCondition(), 100);
}

void loop() {
    taskManager.runLoop();
}
*/

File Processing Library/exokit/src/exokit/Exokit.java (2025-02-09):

package exokit;

import processing.serial.Serial;

public class Exokit {
	public enum ArmSide {
		LEFT("left"), RIGHT("right");
		
		final String serialName;
		private ArmSide(String serialName) {
			this.serialName = serialName;
		}
	}
	
	public enum JointType {
		ELBOW("elbow"), SHOULDER_SIDE("shoulderside"), SHOULDER_BACK("shoulderback");
		
		final String serialName;
		private JointType(String serialName) {
			this.serialName = serialName;
		}
	}
	
	public enum JointMovementDirection {
		ABDUCTION_OR_FLEXION("abduction"), ADDUCTION_EXTENSION("adduction"), BOTH("both");
		
		final String serialName;
		private JointMovementDirection(String serialName) {
			this.serialName = serialName;
		}
	}
	
	public enum Gesture {
		WAVE("wave");
		
		final String serialName;
		private Gesture(String serialName) {
			this.serialName = serialName;
		}
	}
	
	public enum MoveToTargetType {
		ABSOLUTE("absolute"), RELATIVE("relative");
		
		final String serialName;
		private MoveToTargetType(String serialName) {
			this.serialName = serialName;
		}
	}
	
	private Serial serial;
	
	Exokit(Serial serial) {
		this.serial = serial;
	}
	
	public void armAmplify(int exoId, ArmSide side, float torquePercentage) {
		armAmplify(exoId, side, torquePercentage, JointMovementDirection.BOTH, 30, 0);
	}
	
	public void armAmplify(int exoId, ArmSide side, float torquePercentage, JointMovementDirection amplifyDirection) {
		armAmplify(exoId, side, torquePercentage, amplifyDirection, 30, 0);
	}
	
	public void armAmplify(int exoId, ArmSide side, float torquePercentage, JointMovementDirection amplifyDirection, int startingVelocity) {
		armAmplify(exoId, side, torquePercentage, amplifyDirection, startingVelocity, 0);
	}
	
	public void armAmplify(int exoId, ArmSide side, float torquePercentage, JointMovementDirection amplifyDirection, int startingVelocity, int maxVelocity) {
		serial.write("armamplify " + exoId + " " + side.serialName + " " + torquePercentage + " " + amplifyDirection.serialName + " " + startingVelocity+ " " + maxVelocity + "\n");
	}
	
	public void armConstrainTo(int exoId, ArmSide side, ExoArmAngles angles, float radius) {
		serial.write("armconstrainto " + exoId + " " + side.serialName + " " + angles.toSerialString() + " " + radius + "\n");
	}
	
	public void armFilterSpeed(int exoId, ArmSide side, float minVelocity, float maxVelocity, JointMovementDirection onDirection) {
		armFilterSpeed(exoId, side, minVelocity, maxVelocity, onDirection, 0.05f, 0.05f, 0.05f, 0.05f);
	}
	
	public void armFilterSpeed(int exoId, ArmSide side, float minVelocity, float maxVelocity, JointMovementDirection onDirection, float amplifyFlexTorquePercentage) {
		armFilterSpeed(exoId, side, minVelocity, maxVelocity, onDirection, amplifyFlexTorquePercentage, 0.05f, 0.05f, 0.05f);
	}
	
	public void armFilterSpeed(int exoId, ArmSide side, float minVelocity, float maxVelocity, JointMovementDirection onDirection, float amplifyFlexTorquePercentage, 
			float resistFlexTorquePercentage) {
		armFilterSpeed(exoId, side, minVelocity, maxVelocity, onDirection, amplifyFlexTorquePercentage, 
				resistFlexTorquePercentage, 0.05f, 0.05f);
	}
	
	public void armFilterSpeed(int exoId, ArmSide side, float minVelocity, float maxVelocity, JointMovementDirection onDirection, float amplifyFlexTorquePercentage, 
			float resistFlexTorquePercentage, float amplifyExtensionTorquePercentage) {
		armFilterSpeed(exoId, side, minVelocity, maxVelocity, onDirection, amplifyFlexTorquePercentage, 
				resistFlexTorquePercentage, amplifyExtensionTorquePercentage, 0.05f);
	}
	
	public void armFilterSpeed(int exoId, ArmSide side, float minVelocity, float maxVelocity, JointMovementDirection onDirection, float amplifyFlexTorquePercentage, 
			float resistFlexTorquePercentage, float amplifyExtensionTorquePercentage, float  resistExtensionTorquePercentage) {
		serial.write("armfilterspeed " + exoId + " " + side.serialName + " " + minVelocity + " " + maxVelocity + " " + onDirection.serialName + " " + amplifyFlexTorquePercentage
				+ " " + resistFlexTorquePercentage + " " + amplifyExtensionTorquePercentage + " " + resistExtensionTorquePercentage + "\n");
	}
	
	public void armGesture(int exoId, ArmSide side) {
		armGesture(exoId, side, Gesture.WAVE);
	}
	
	public void armGesture(int exoId, ArmSide side, Gesture gesture) {
		serial.write("armgesture " + exoId + " " + side.serialName + " " + gesture.serialName + "\n");
	}
	
	public void armGuideAway(int exoId, ArmSide side, ExoArmAngles armAngles, float radius) {
		armGuideAway(exoId, side, armAngles, radius, 0.05f, 0.05f);
	}
	
	public void armGuideAway(int exoId, ArmSide side, ExoArmAngles armAngles, float radius, float amplifyTorquePercentage) {
		armGuideAway(exoId, side, armAngles, radius, amplifyTorquePercentage, 0.05f);
	}
	
	
	public void armGuideAway(int exoId, ArmSide side, ExoArmAngles armAngles, float radius, float amplifyTorquePercentage, float resistTorquePercentage) {
		serial.write("armguideaway " + exoId + " " + side.serialName + " " + armAngles.toString() + " " + radius + " " + amplifyTorquePercentage + " " + resistTorquePercentage + "\n");
	}
	
	public void armGuideTowards(int exoId, ArmSide side, ExoArmAngles armAngles, float radius) {
		armGuideTowards(exoId, side, armAngles, radius, 0.05f, 0.05f);
	}
	
	public void armGuideTowards(int exoId, ArmSide side, ExoArmAngles armAngles, float radius, float amplifyTorquePercentage) {
		armGuideTowards(exoId, side, armAngles, radius, amplifyTorquePercentage, 0.05f);
	}
	
	
	public void armGuideTowards(int exoId, ArmSide side, ExoArmAngles armAngles, float radius, float amplifyTorquePercentage, float resistTorquePercentage) {
		serial.write("armguidetowards " + exoId + " " + side.serialName + " " + armAngles.toString() + " " + radius + " " + amplifyTorquePercentage + " " + resistTorquePercentage + "\n");
	}
	
	public void armJerk(int exoId, ArmSide side, float minJerkAngle, float maxJerkAngle, int minJerkIntervalMs, int maxJerkIntervalMs, float maxAccumulatedMovementsLeft, float maxAccumulatedMovementsRight) {
		serial.write("armjerk " + exoId + " " + side.serialName + " " + minJerkAngle + " " + maxJerkAngle + " " + minJerkIntervalMs
				+ " " + maxJerkIntervalMs + " " + maxAccumulatedMovementsLeft + " " + maxAccumulatedMovementsRight + "\n");
	}
	
	public void armLock(int exoId, ArmSide side) {
		serial.write("armlock " + exoId + " " + side.serialName + "\n");
	}
	
	public void armMirror(int sourceExoId, ArmSide sourceArmSide, int targetExoId, ArmSide targetArmSide, boolean mirrorElbow, boolean mirrorShoulderSide,
			boolean mirrorShoulderBack) {
		armMirror(sourceExoId, sourceArmSide, targetExoId, targetArmSide, mirrorElbow, mirrorShoulderSide,
				mirrorShoulderBack, 1.0f, 1.0f, 1.0f);
	}
	
	public void armMirror(int sourceExoId, ArmSide sourceArmSide, int targetExoId, ArmSide targetArmSide, boolean mirrorElbow, boolean mirrorShoulderSide,
			boolean mirrorShoulderBack, float scaleFactorElbow) {
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
